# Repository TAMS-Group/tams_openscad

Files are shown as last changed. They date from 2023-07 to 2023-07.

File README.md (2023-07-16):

# tams_openscad

OpenSCAD models and libraries used with our robots.

This package collects 3D-models of robot parts, sensors, and
mechanical components to be used with the OpenSCAD 3D-modelling tool.
Feel free to use and modify as needed for your own robots and tools.

In particular, this package includes a set of common "TAMS flange"
adapter plates that we use to quickly assemble combinations of sensors 
and grippers or specialized tools for experiments. 
The basic idea is to combine a <em>core</em> part permanently 
installed on a robot (or fixed assembly) with different <em>outer</em>
adapter plates for different grippers or experiment setups.

<a href="doc/images/tams_flange_kuka_wsg50.png">
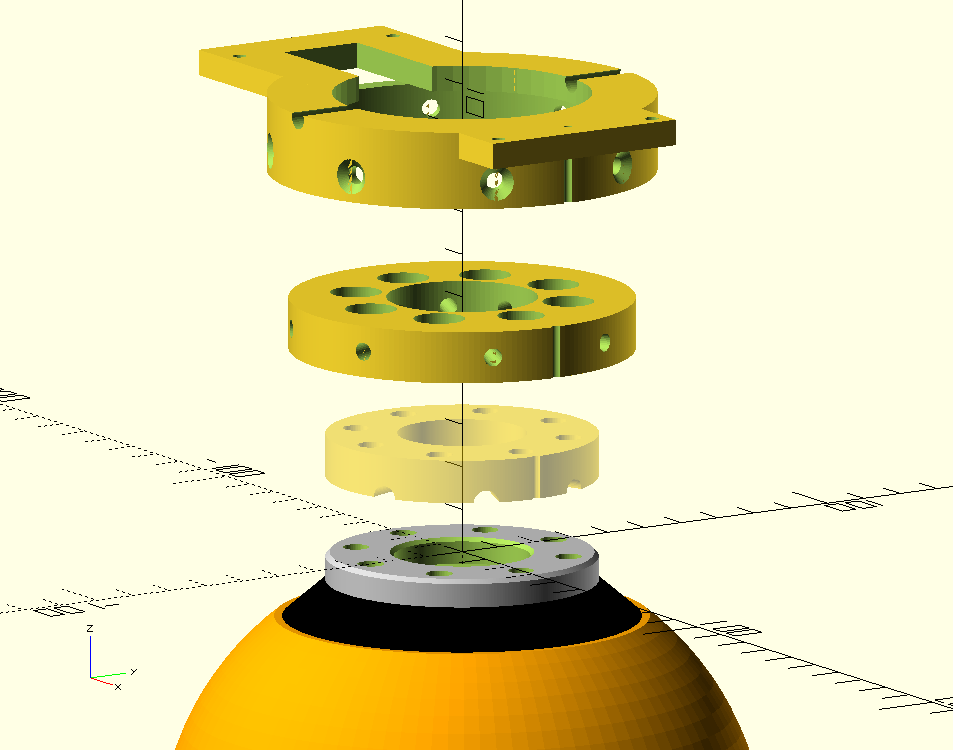
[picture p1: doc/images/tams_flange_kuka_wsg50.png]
TAMS flange adapter for Schunk WSG-50 gripper on Kuka LWR-4+robot
  
</a>

<a href="doc/images/tams_flange_diana_gripper.png">
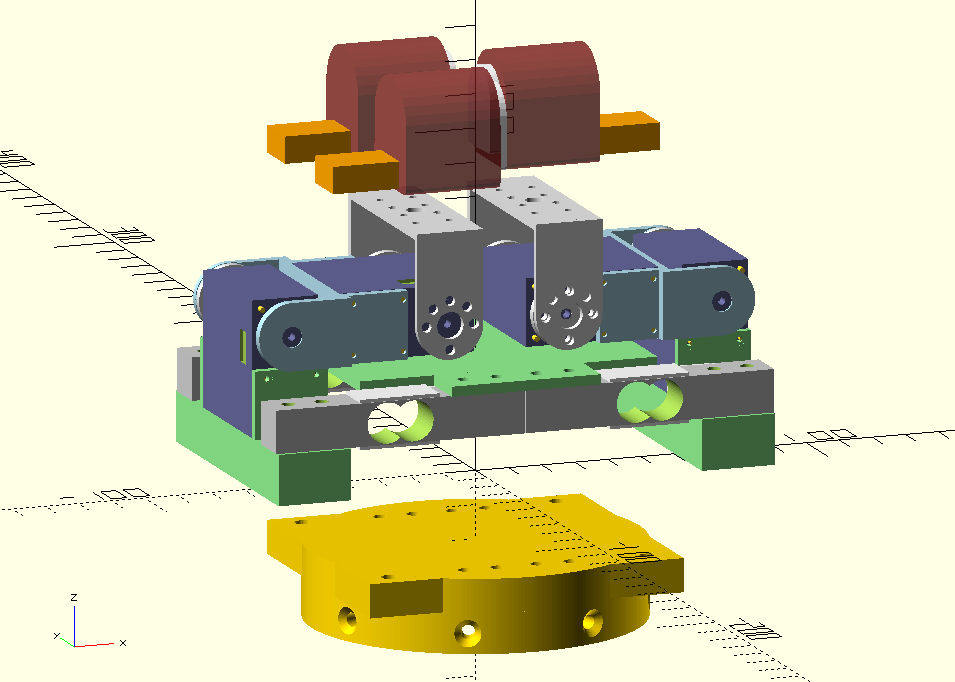
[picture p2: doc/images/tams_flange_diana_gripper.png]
TAMS flange adapter for SCSERVO driven 4-DOF two-finger grippr
  
</a>

We currently use a common size of d=80mm and h=12mm for the core adapters,
which fits the ISO-9409-1-50-4-M6 adapter used on most current cobots
(UR5/UR5e, UR10/UR10e, Kuka LWR4+ iiwa, ...) and the slightly larger
ISO-9409-1-63-4-M6 flange on our Mitsubishi PA10-6C robots.
The outer adapters typically use d=99mm and varying height, depending
on expected payload and tool mounting requirements.

Outer and inner parts are connected with a set of eight radial M4 screws,
so that parts can be mounted or unmounted without disassembly of other
stages or the total robot setup.

There is nothing magical about the values, but they seemed like a promising
combination of required strength/payload and overall size.
To save overall length of the stacked adapters, parts include cavities
to fit the screws/bolts/nuts of the next level.

## Components Overview

This package includes the following <em>core</em> (robot-side) parts:

- UR5/UR5e, UR10/UR10e, LWR4+, iiwa, ... (ISO-9409-1-50-4-M6) flange adapter,
  in three variants: with embedded M4 square nuts, embedded M4 hex nuts,
  or without embedded nuts. The version without embedded nuts is easiest
  to use, but be careful not to over-torque the radial mounting screws.
- Mitsubishi PA10-6C (ISO-9409-1-63-4-M6) flange adapter.
- 3D-printed ISO-9409-1-50-4-M6 compatible adapter (to stack things).

<a href="doc/images/tams_flange_ur5.png">
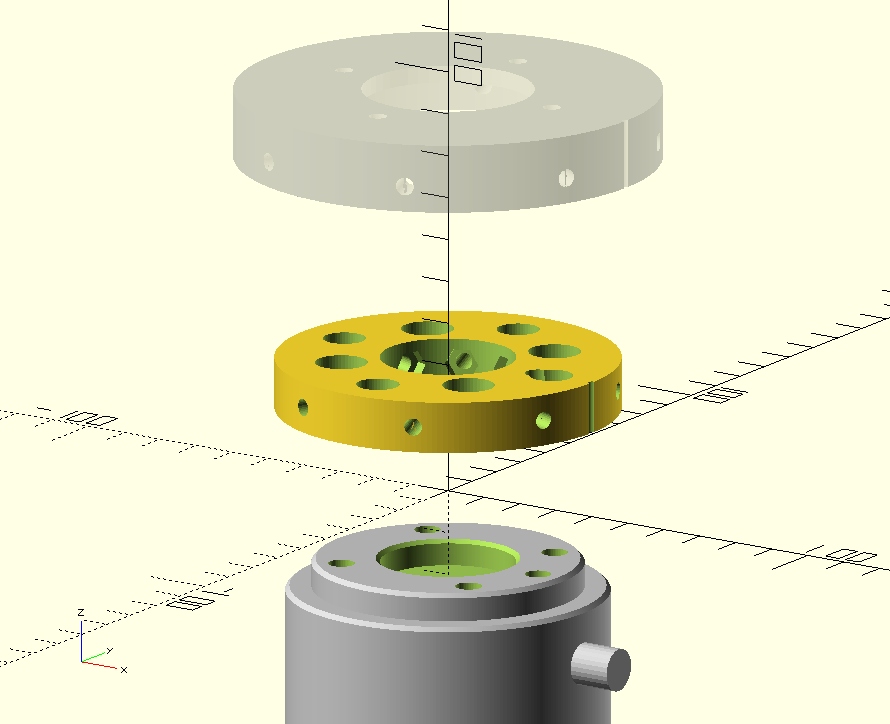
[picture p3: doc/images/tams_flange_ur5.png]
TAMS flange adapter for UR5/UR5e industrial robot
  
</a>

<a href="doc/images/tams_flange_pa10.png">
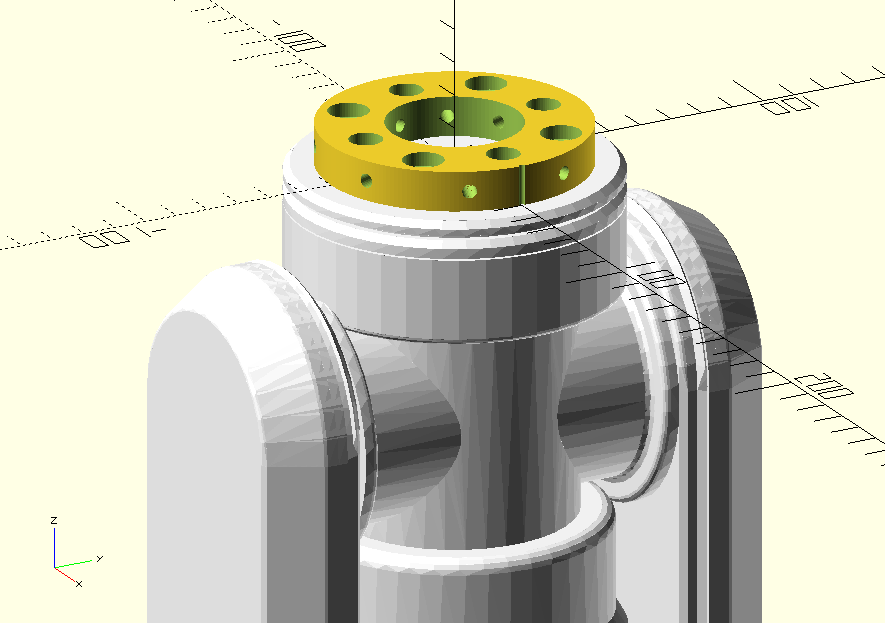
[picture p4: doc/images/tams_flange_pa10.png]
TAMS flange adapter for MHI PA10-6C industrial robot
  

</a>

Force/Torque-sensor (tool-side) <em>core</em> adapters:

- ATi Mini45e.
- Robotiq FTS-150 (soon).
- Sunrise Instruments M3207.

And the corresponding <em>outer</em> adapters for the following tools:

- ATi Nano17e force/torque sensor.
- ATi Mini45e force/torque sensor.
- Robotiq FTS-150 force/torque sensor (soon).
- Sunrise Instruments M3207 force/torque sensor.
- passive weight holder for force/torque sensor calibration.

- Robotiq 3-finger adaptive gripper (aka 3-finger hand).
- Schunk WSG-50 parallel gripper.
- TAMS in-house SCSERVO 4-DOF two-finger gripper.
- TAMS in-house tactile arrays.

- DIGIT tactile sensor.
- generic camera-holder (1/4-inch-20-UNC-thread) (6.35 outer, 5.2mm inner, thread 1.27mm).
- fischertechnik-compatible adapter plate.
- ...

<a href="doc/images/tams_flange_ati_mini45.png">
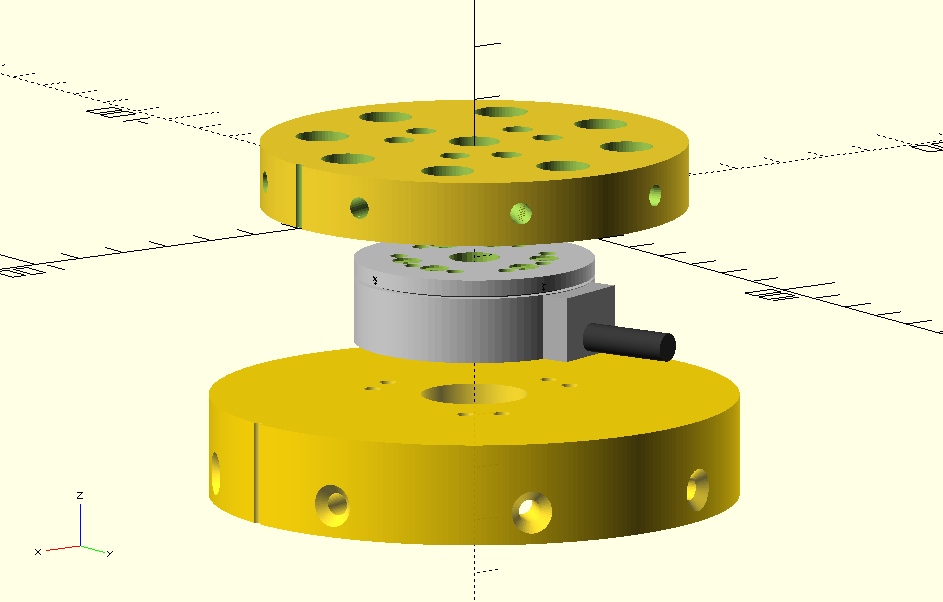
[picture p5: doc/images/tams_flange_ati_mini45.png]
TAMS flange core and outer adapter for ATi mini45e force/torque sensor
  
</a>

<a href="doc/images/tams_flange_fischertechnik.png">
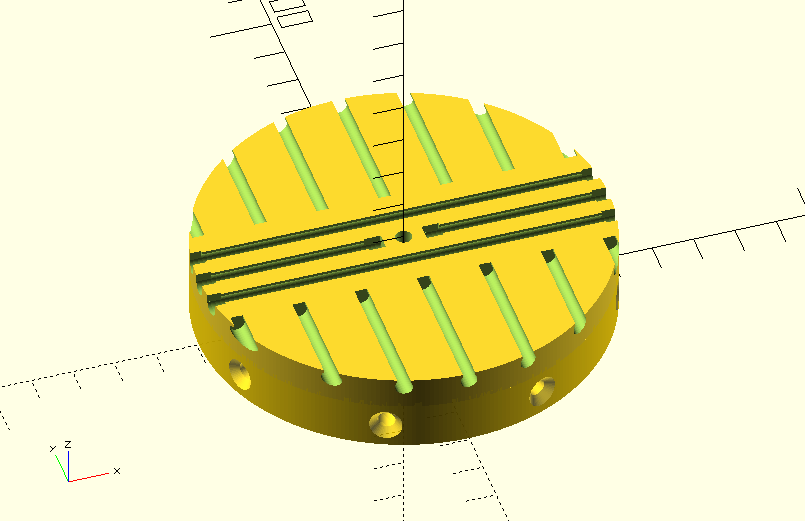
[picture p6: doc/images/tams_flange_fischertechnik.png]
TAMS flange outer adapter for fischertechnik construction set
  
</a>

## Libraries

The package also collects a set of OpenSCAD part libraries that
you might find useful for your own designs:

- <a href="libs/electronics.scad"><tt>electronics.scad</tt></a>,
  a random collection of basic electronic components and common
  Arduino-boards and sensor breakout boards,
- <a href="libs/simple-screws.scad"><tt>simple-screws.scad</tt></a>,
  simplified models of various DIN/ISO-sized screws, nuts, and washers,
- <a href="libs/load_cells.scad"></tt>load_cells.scad</tt></a>,
  geometric models of common load-cells.

<a href="doc/images/electronics.png">
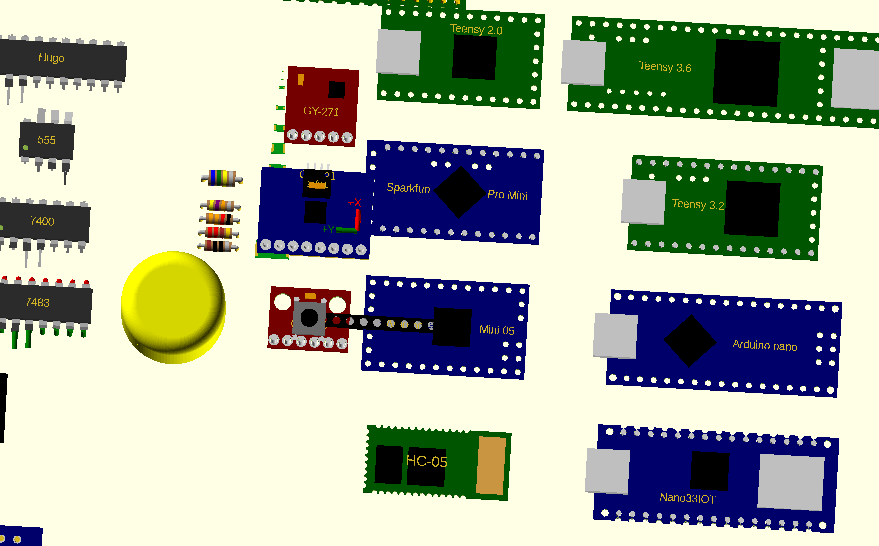
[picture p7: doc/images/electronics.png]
OpenSCAD library of electronics components
  
</a>

<a href="doc/images/load_cells.png">
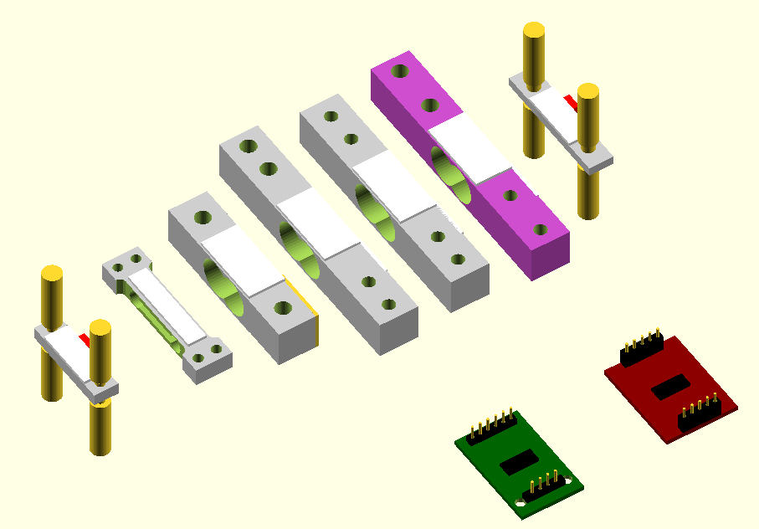
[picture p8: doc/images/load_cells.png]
OpenSCAD library of common load cells
  
</a>

<a href="doc/images/simple_screws.png">
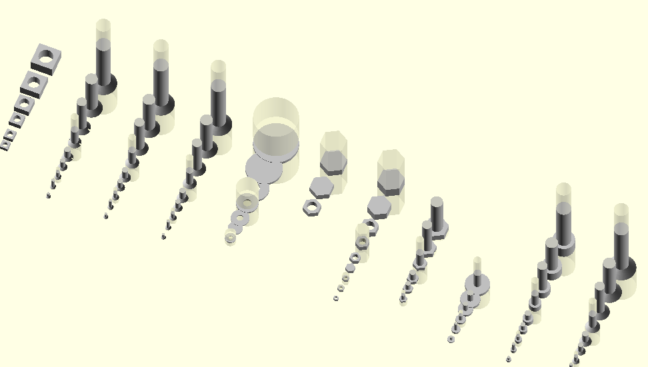
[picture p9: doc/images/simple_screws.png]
OpenSCAD library of DIN/ISO sized screws
  
</a>

## Disclaimer 

In our lab, these plates are used for different short-time experiments,
typically 3D-printed from common PLA/PETG filament with medium infill values. 
However, the parts are clearly not designed for heavy-duty 24/7 industrial use,
and none of the parts have been checked with FEM analysis for mechanical
stress; all dimensions provided just seemed like an acceptable compromise 
for our use cases and relatively low payloads.
In particular, be careful with overloading the parts, as 3D-printed objects
are always prone to delamination and sudden complete breakage.

## Installation

Just download the package. You will need OpenSCAD to open and
modify the provided 3D-models. 
Of course, you will need a 3D-printer to actually produce the adapter plates,
and the usual components (e.g. M3/M4/M6 screws and nuts) to assemble
the different parts.

<!-- preview: grip README.md + firefox localhost:6419 -->

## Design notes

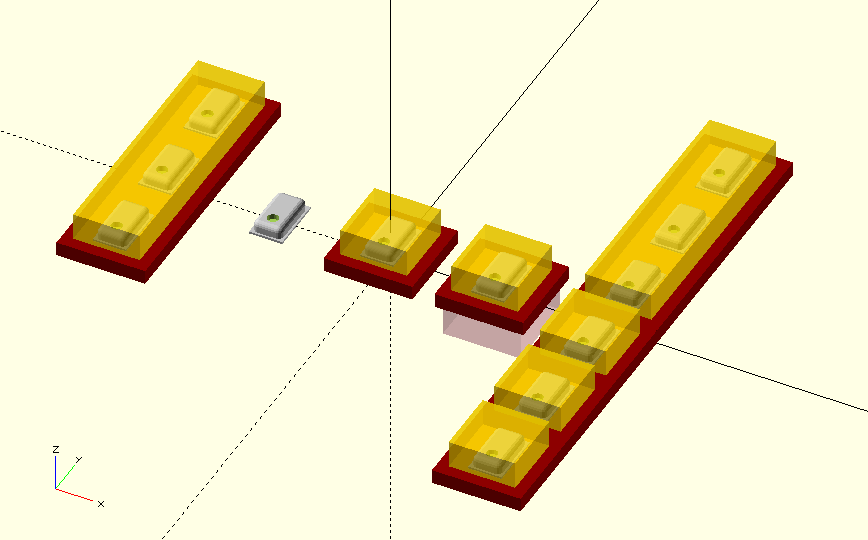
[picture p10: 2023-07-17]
doc/images/takktile.png

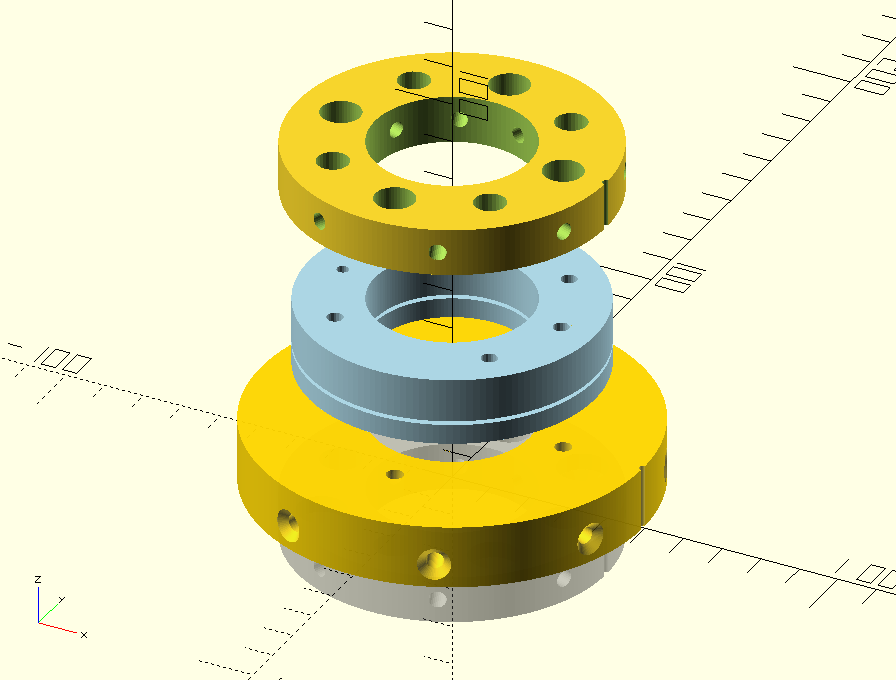
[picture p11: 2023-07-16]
doc/images/tams_flange_sunrise_m3207.png

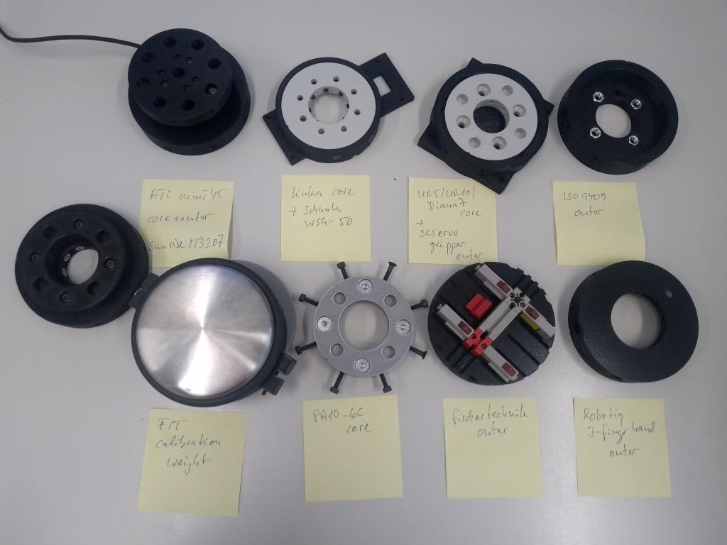
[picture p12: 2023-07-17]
doc/images/tams_flange_family.jpg

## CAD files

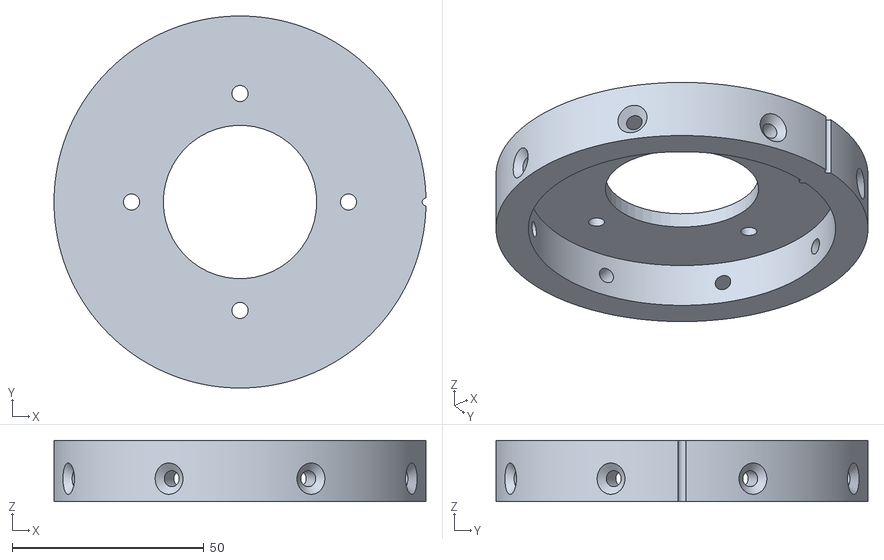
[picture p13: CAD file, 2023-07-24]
meshes/m3207_tams_outer_adapter_80x12_d97.stl
97.0 x 97.0 x 16.0

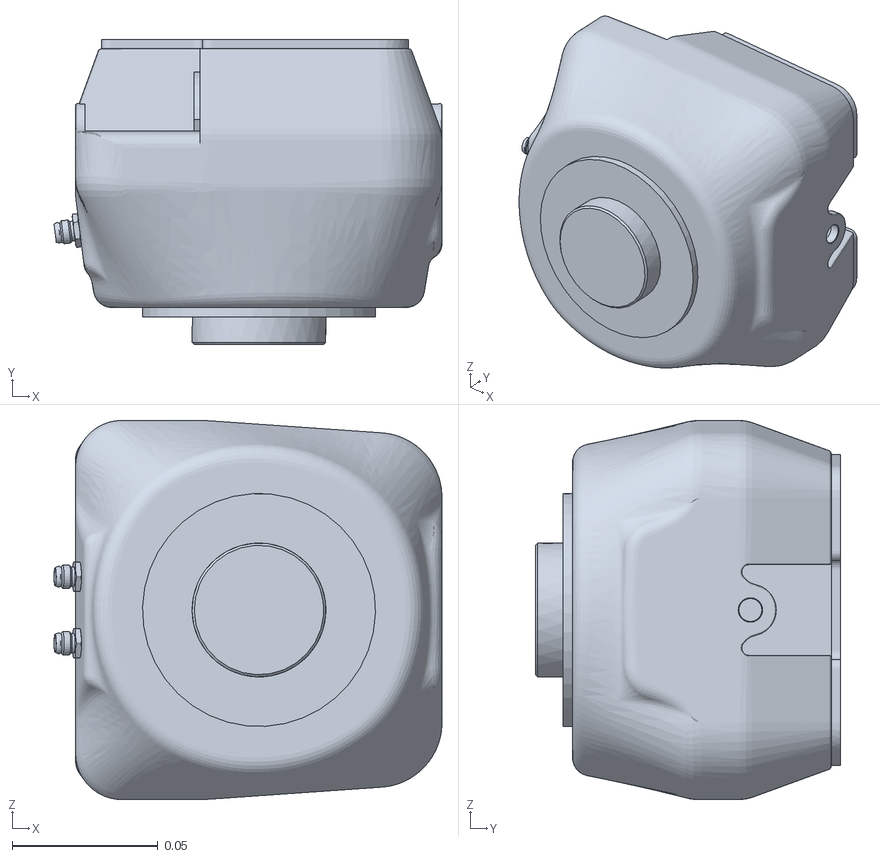
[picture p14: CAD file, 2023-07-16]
robots/robotiq_palm.stl
0.133 x 0.105 x 0.13

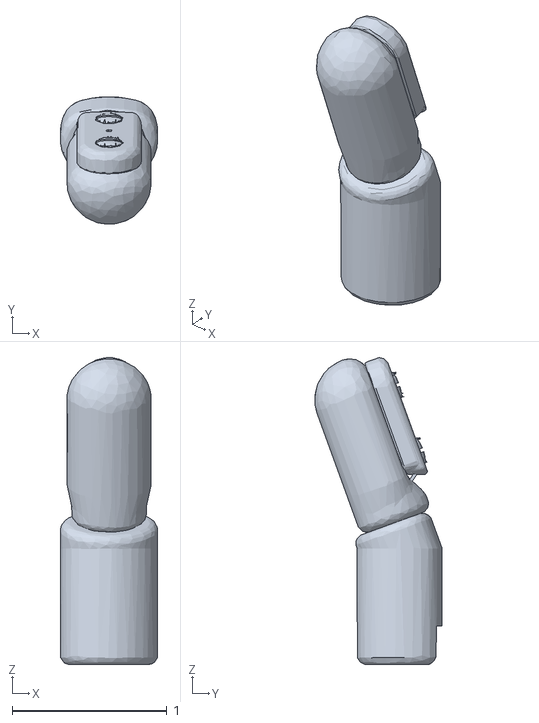
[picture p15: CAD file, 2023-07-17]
sensors/biotac_decimated.stl
0.63 x 0.824 x 1.98

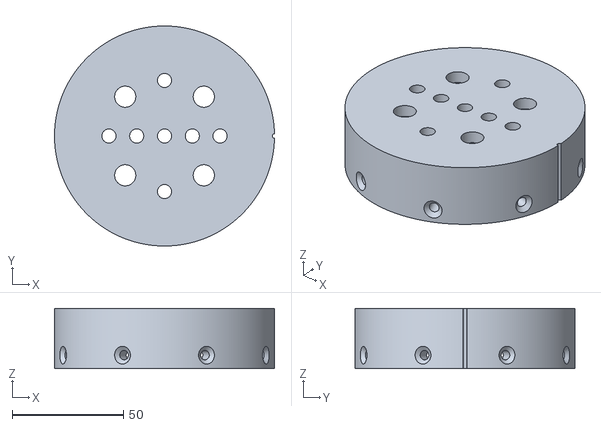
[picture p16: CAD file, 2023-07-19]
meshes/camera_mount_outer_adapter_80x12x15.stl
99.0 x 99.0 x 27.0

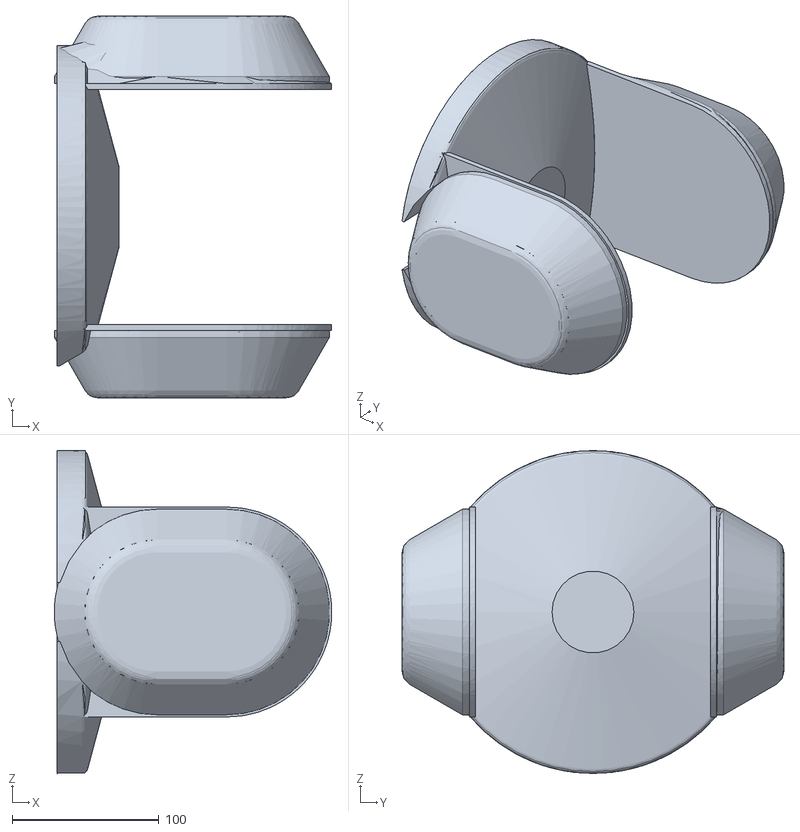
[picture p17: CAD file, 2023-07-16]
robots/pa10s1.stl
189.0 x 260.0 x 220.0

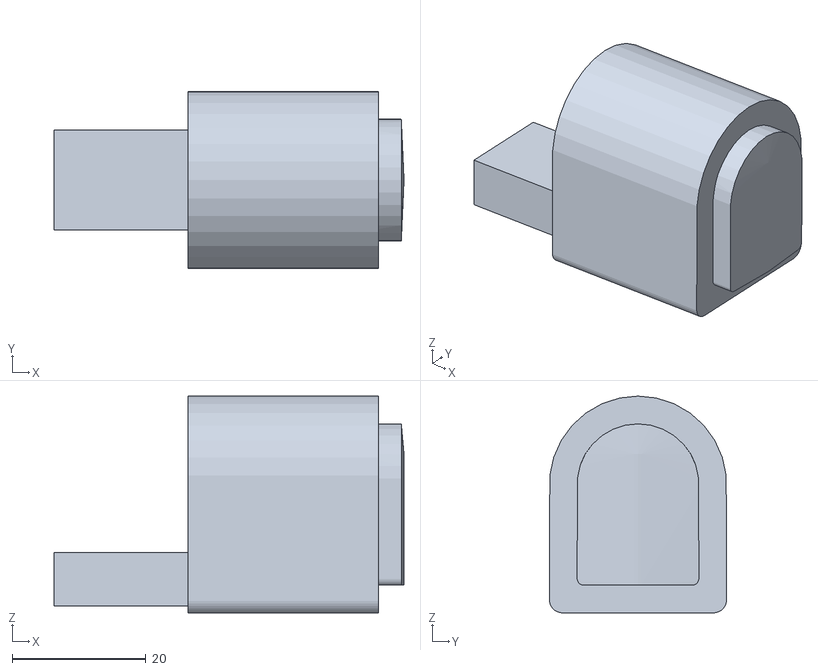
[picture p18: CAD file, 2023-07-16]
sensors/digit_sensor.stl
52.3 x 26.5 x 32.4

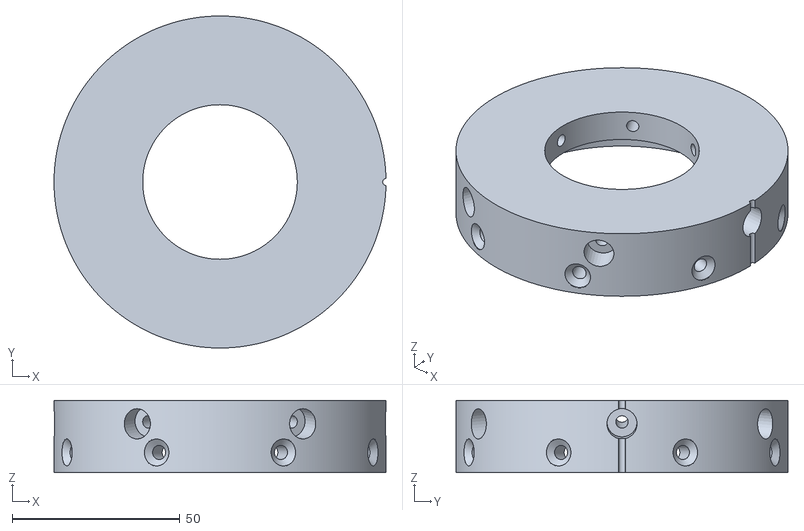
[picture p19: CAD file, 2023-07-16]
meshes/robotiq_3finger_hand_outer_adapter_80x12.stl
99.0 x 99.0 x 21.5

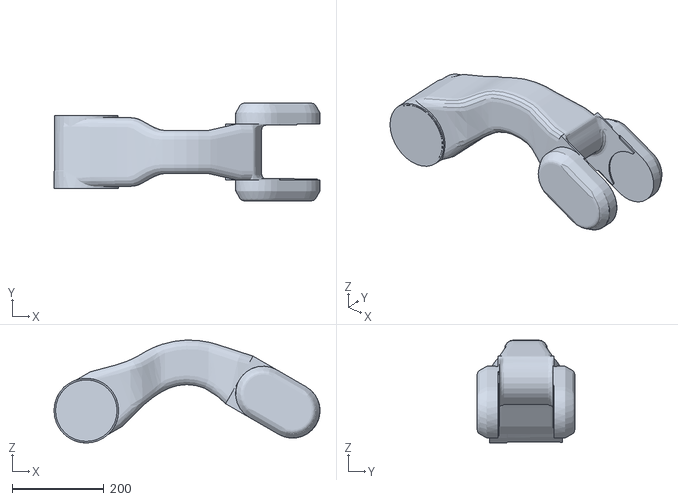
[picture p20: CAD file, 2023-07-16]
robots/pa10s2.stl
580.5 x 213.0 x 224.5

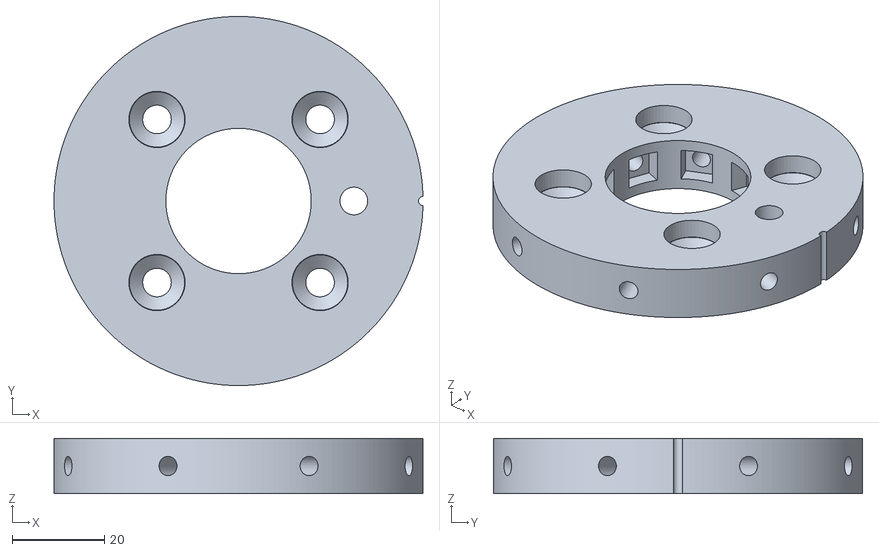
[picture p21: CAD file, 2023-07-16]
meshes/ur5_tams_flange_adapter_80x12_square_nuts.stl
80.0 x 80.0 x 12.0

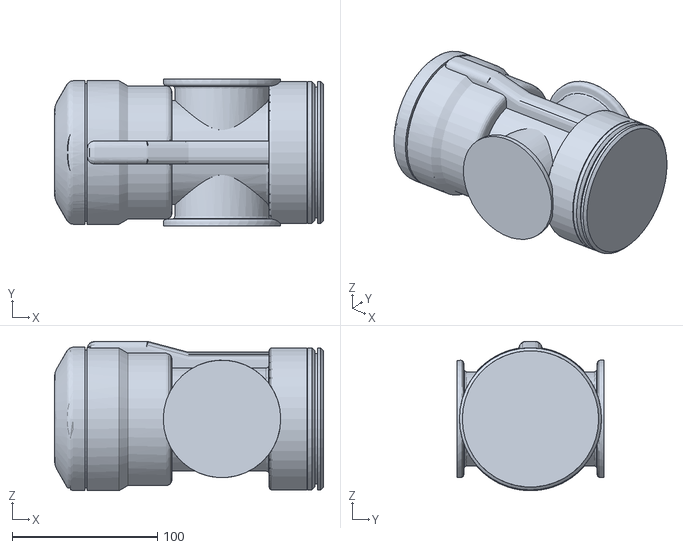
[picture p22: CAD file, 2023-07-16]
robots/pa10w1.stl
185.5 x 101.4 x 103.0

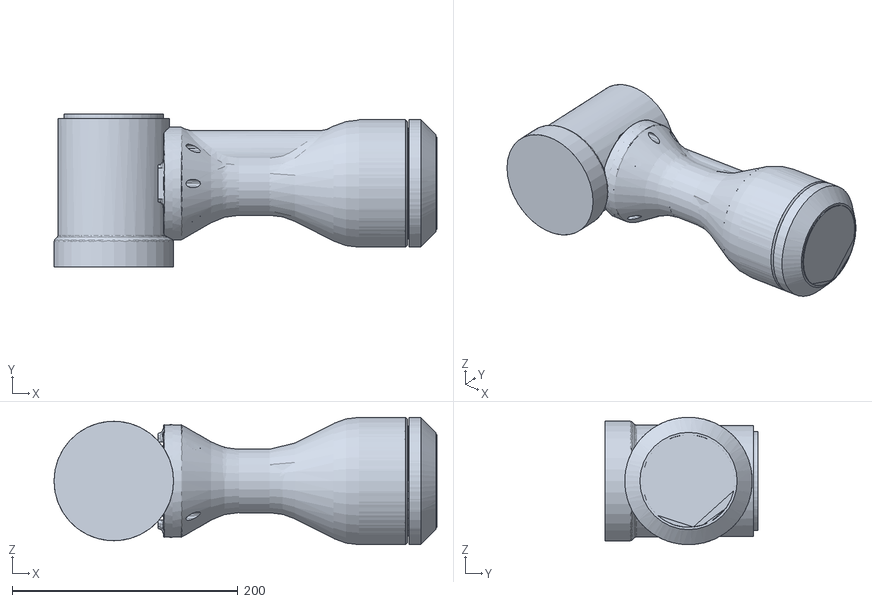
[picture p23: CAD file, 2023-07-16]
robots/pa10e1.stl
339.5 x 135.5 x 112.9

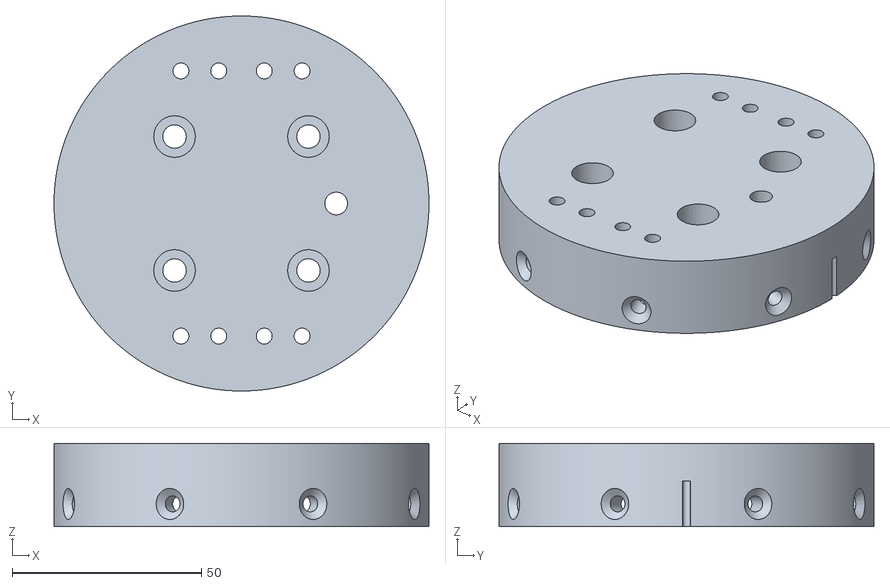
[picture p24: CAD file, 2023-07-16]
meshes/diana_gripper_outer_round_80x12.stl
99.0 x 99.0 x 22.0

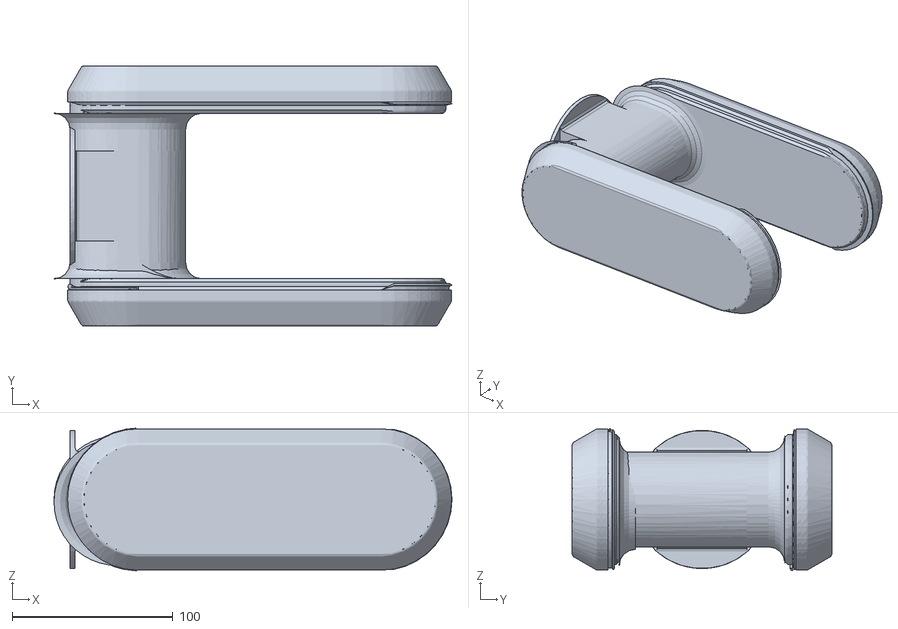
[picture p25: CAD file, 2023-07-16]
robots/pa10e2.stl
247.8 x 162.0 x 88.9

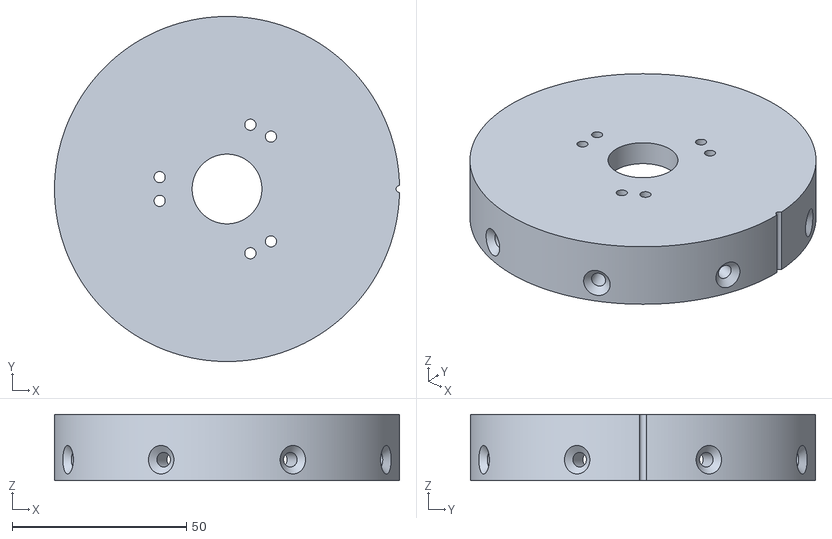
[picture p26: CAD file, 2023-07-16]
meshes/ati45_flange_outer_adapter_80x12x7.stl
99.0 x 99.0 x 19.0

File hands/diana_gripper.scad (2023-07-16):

/** simple four-servo two-finger gripper with mountplate for
 * "TAMS flange" and UR5/Diana7 robots (ISO-9409-...).
 *
 * 2023.07.13 - add "extra_bores" to match our existing (modified) prototype
 * 2022.07.01 - export first meshes (v1)
 * 2022.07.01 - created (based on feetech-servo-hand.scad)
 *
 * (c) 2021, 2022, 2023 fnh, hendrich@informatik.uni-hamburg.de
 */

use <../robots/ur5_flange.scad>
use <../robots/ur5_tams_flange_adapter.scad>
use <../robots/tams_flange_outer_adapter.scad>

use <../sensors/feetech_servo.scad>
use <../sensors/digit_sensor.scad>
use <../libs/load_cells.scad>


translate( [0,0,-100] ) 
  ur5_tool_flange();

color( "red", 0.8 )
rotate( [0,0,0] ) translate( [0,0,-75] ) 
  ur5_tams_flange_adapter( extra_cavities=[0] );




fn = 100;
eps = 0.01;
M6_bore = 6.2;
M4_bore = 4.2;
ee = 30; // "explosion" distance

ddx = 75/2 + 0.2;
ddy = 35;
ddz = 15 + 5 + 12.7/2;

make_diana_flange = 0;
make_gripper_base = 0;

//translate( [0,0,1] ) 
//gripper_base_tams_riser_blocks();
make_gripper_base_tams = 1;

make_palm_plate   = 1;
make_servo_base1  = 1; // first finger
make_connector1   = 1;

make_servo_base2  = 1; // second finger
make_connector2   = 1;

show_loadcells    = 1;

show_servo1P      = 1; // first finger, proximal
show_servo1D      = 1; // first finger, distal
show_bracket1     = 1; // first finger, distal mounting bracket
show_digit1       = 1; // first finger, DIGIT sensor

show_servo2P      = 1; // second finger, proximal
show_servo2D      = 1; // second finger, distal
show_bracket2     = 1; // second finger, distal mounting bracket
show_digit2       = 1; // second finger, DIGIT sensor

if (make_diana_flange) diana_flange();
if (make_gripper_base) gripper_base();

if (make_gripper_base_tams) translate( [0,0,-ee] ) 
  color( "gold" )
  gripper_base_tams();


color( "lightgreen" ) {
if (make_palm_plate)   translate( [0,0, 15+5+12.7] ) palm_plate();
if (make_servo_base1)  translate( [75.0-6-5,0,20] ) servo_base();
if (make_servo_base2)  translate( [-75.0+6+5,0,20] ) servo_base();
}               


if (show_loadcells) {
translate( [ ddx,  ddy, ddz] ) load_cell_komputer_10kg();   
translate( [-ddx,  ddy, ddz] ) load_cell_komputer_10kg();   
translate( [ ddx, -ddy, ddz] ) load_cell_komputer_10kg();   
translate( [-ddx, -ddy, ddz] ) load_cell_komputer_10kg();   
}

if (show_servo1P) {
translate( [75-10,20,50] ) rotate( [0,90,90] ) feetech_scs20_servo( extrude_21mm_axles=0);
translate( [75-10,20+6,50] ) rotate( [0,90,-90] ) feetech_servo_disc( extrude_screws_length=0, extrude_screws_head=[] );
// translate( [75-10,-20-6,50] ) rotate( [0,90,90] ) feetech_servo_disc( extrude_screws_length=0, extrude_screws_head=[] );
}

if (make_connector1) 
translate( [45,1,50] ) rotate( [-90,0,-90] ) // for complete model
// rotate( [-90,0,-90] ) translate( [0,0,-20] ) // for standalone rendering
proximal_medial_connector();

if (show_servo1D) {
translate( [75-10-47,20,50] ) rotate( [-90,0,0] ) feetech_scs20_servo( extrude_21mm_axles=0);
translate( [75-10-47,20+6,50] ) rotate( [0,90,-90] ) feetech_servo_disc( extrude_screws_length=0, extrude_screws_head=[] );
translate( [75-10-47,-20-6,50] ) rotate( [0,90,90] ) feetech_servo_disc( extrude_screws_length=0, extrude_screws_head=[] );
}

if (show_bracket1) 
  translate( [18,0,15+5+30+27.5] ) rotate( [0,180,90] ) 
    feetech_scs_bracket_big();

if (show_digit1) 
translate( [ 18,0,90] ) rotate( [0,0,180]) 
digit_sensor();


if (show_servo2P) {
translate( [-(75-10),20,50] ) rotate( [0,90,90] ) feetech_scs20_servo( extrude_21mm_axles=0);
translate( [-(75-10),20+6,50] ) rotate( [0,90,-90] ) feetech_servo_disc( extrude_screws_length=0, extrude_screws_head=[] );
// translate( [-(75-10),-20-6,50] ) rotate( [0,90,90] ) feetech_servo_disc( extrude_screws_length=0, extrude_screws_head=[] );
}

if (make_connector2) 
translate( [-45,1,50] ) rotate( [90,0,-90] ) proximal_medial_connector();

if (show_servo2D) {
translate( [-(75-10-47),20,50] ) rotate( [-90,180,0] ) feetech_scs20_servo( extrude_21mm_axles=0);
translate( [-(75-10-47),20+6,50] ) rotate( [0,90,-90] ) feetech_servo_disc( extrude_screws_length=0, extrude_screws_head=[] );
// translate( [-(75-10-47),-20-6,50] ) rotate( [0,90,90] ) feetech_servo_disc( extrude_screws_length=0, extrude_screws_head=[] );
}

if (show_bracket2) 
translate( [-18,0,15+5+30+27.5] ) rotate( [0,180,90] ) feetech_scs_bracket_big();

if (show_digit2) {
translate( [-18,-20,90] ) digit_sensor();
translate( [-18,+20,90] ) digit_sensor();
}

/**
 * hardcoded size palm plate, mounts on load-cell screws
 */
module palm_plate( 
  alpha = 0.9,
  dx = 45, dy = 85, dz = 3, dx2=90,
  load_cell = [75.0, 12.7, 12.7],
  bore_offsets = [-16, -6, 6, 16], // relative to center of palm
  M4_bore=4.2, M4_head_diameter = 7.0+1.0, M4_head_length=4+1.0, M4_screw_length=30, 
)
{
  difference() {
    union() {
      translate( [0,0,dz/2] ) 
        cube( [dx, dy, dz], center=true );
      translate( [0,0,dz/2] ) 
        cube( [dx2, dy-2*15, dz], center=true );
    }
    
     // loadcell mounting bores
    for( ddy=[-35, +35] ) { // loadcell y positions
      for( ddx=bore_offsets ) { // loadcell M4 bores
        translate( [ddx, ddy, -dz-eps] ) 
          cylinder( d=M4_bore, h=dz+ddz+2*eps, center=false, $fn=50 );
        translate( [ddx, ddy, -dz-eps] ) 
          cylinder( d=M4_head_diameter, h=M4_head_length, center=false, $fn=50 );
      }
    }

  }
}


module servo_base(
  alpha = 0.9,
  dx = 6+10+6, dy = 85, dz = 15, ddy = 35,
  dty = 2.5, // thickness of servo mounting "towers"
  servoy = 41.1, // some SCservos are slightly wider than 40.0
  load_cell = [75.0, 12.7, 12.7],
  bore_offsets = [-5, 5], // relative to center of servo_base block!
  M4_bore=4.2, M4_head_diameter = 7.0+1.0, M4_head_length=4+1.0, M4_screw_length=30, 
)
{
  difference() {
    union() {
      // main mounting block
      color( "gold", alpha )
      translate( [0,0,-dz/2] )
        cube( [dx,dy,dz], center=true );
      
      // servo mounting "towers"
      color( "gold", alpha )
      for( ddty=[-servoy/2-dty/2, servoy/2+dty/2] ) 
        translate( [0, ddty,10] )
          cube( [dx, dty, 20], center=true );      
    }
    
    // loadcell mounting bores
    for( ddy=[-35, +35] ) { // loadcell y positions
      for( ddx=[-5, 5] ) { // loadcell M4 bores
        translate( [ddx, ddy, -dz-eps] ) 
          cylinder( d=M4_bore, h=dz+ddz+2*eps, center=false, $fn=50 );
        translate( [ddx, ddy, -dz-eps] ) 
          cylinder( d=M4_head_diameter, h=M4_head_length, center=false, $fn=50 );
      }
    }
    
    // servo mounting bores
    translate( [0,20,30-eps] ) rotate( [0,90,90] ) feetech_scs20_servo( extrude_mounting_screws=dty, extrude_mounting_screws_heads=4 
    );
  }
}


module gripper_base(
  alpha = 0.9,
  dx = 90, dy = 85, dz = 15,
  M6_bore=6.2, M6_head_diameter = 10.0+1.0, M6_head_length=7+1.0, M6_screw_length=20,
  M4_bore=4.2, M4_head_diameter = 7.0+1.0, M4_head_length=4+1.0, M4_screw_length=30,
  make_ISO9409_bores = false,
  extra_bores = [[38,36,5],[-39,36,5], [-39,-36,5],[39,-36,5]], // [[x,y,d],[x,y,d],[x,y,d], ...
)
{
  difference() {
    color( "lightgreen", alpha )
    union() {
      // mounting plate for Diana7 flange
      translate( [0,0,dz/2] )
        cube( [dx,dy,dz], center=true );
      
      // riser blocks to mount loadcells, min z-height 3mm for loadcell clearance
      ddz = 5;
      for( dyy =[dy/2-16/2,-dy/2+16/2] )
        translate( [0, dyy,dz+ddz/2] )
          cube( [23+23, 16, ddz], center=true );
    }
    
    // Diana7 M6 D912 screw bores, max length in flange is 12 
    rr = 25.0; 

    if (make_ISO9409_bores) {
      for( phi=[0,90,180,270] ) {
        rotate( [0,0,phi+45] ) translate( [rr,0,-eps] )
          cylinder( d=M6_bore, h=dz+2*eps, center=false, $fn=40 );
        rotate( [0,0,phi+45] ) translate( [rr,0,dz-M6_head_length] )
          cylinder( d=M6_head_diameter, h=M6_head_length+2*eps, center=false, $fn=40 );
      }
    }

    // Diana7 alignment pin bore, max depth in flange in 6
    translate( [rr,0,-eps] )
      cylinder( d=6.0, h=dz+2*eps, center=false, $fn=40 );
    
    // loadcell mount bores
    for( ddy=[-35, +35] ) { // loadcell y positions
      for( ddx=[-16,-6, 6,16] ) { // loadcell M4 bores
        translate( [ddx, ddy, -eps] ) 
          cylinder( d=M4_bore, h=dz+ddz+2*eps, center=false, $fn=50 );
        translate( [ddx, ddy, -eps] ) 
          cylinder( d=M4_head_diameter, h=M4_head_length, center=false, $fn=50 );
      }
    }

    for( i=[0:len(extra_bores)-1] ) {
      echo( "EXTRA_BORES: ", extra_bores[i] );
      ddx = extra_bores[i][0];
      ddy = extra_bores[i][1];
      ddd = extra_bores[i][2];
      translate( [ddx, ddy, -eps] )
        cylinder( d=ddd, h=dz+5, center=false, $fn=40 );
    }
    
  } // difference
}
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

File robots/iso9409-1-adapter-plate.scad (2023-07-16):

/** OpenSCAD model of the ISO-9409-1-50-4-M6 adapter plate,
 * as used on many industrial cobots, e.g. UR3/UR5/UR10, Kuka LWR, ...
 *
 * Based on mechanical drawings from UR documents, plus a low-res scan
 * from research-gate. Dimensions in millimeters.
 * 
 * 2023.03.01 - created
 *
 * (c) 2023 fnh, hendrich@informatik.uni-hamburg.de
 */
 
eps = 0.1;
fudge = 0.1; // FDM overextrusion/shrinking compensation

D1 = 50;   // diameter of screw-bore ring
D2 = 63.0; // outer mounting flange diameter
D3 = 31.5; // diameter of inner bore of mounting flange
N  = 4;    // number of bores
D4 = 6.1;  // M6

translate( [0,0,-15] ) iso9409_1_flange();
translate( [0,0, 15] ) iso9409_1_spacer_ring(); 

 


/* 50-4-M6 robot flange, e.g. LWR-4+, 6mm deep thread bores */
module iso9409_1_flange( D5=90, thickness=15.0, fn=500 ) {
  difference() {
    // main robot tool-flange body
    union() {
      translate( [0,0,0] )
        cylinder( d=90.0, h=thickness-5.0, center=false, $fn=fn );
      translate( [0,0,0] )
        cylinder( d=D2, h=thickness-1, center=false, $fn=fn );     
      translate( [0,0,thickness-1] )
        cylinder( d1=D2, d2=D2-1, h=1, center=false, $fn=fn );     
    }
    // inner bore and extra bevel
    translate( [0,0,thickness+eps-5.0] )
      cylinder( d=D3, h=5.0, center=false, $fn=fn );
    translate( [0,0,thickness+eps-1] )
      cylinder( d1=D3, d2=D3+1, h=1, center=false, $fn=fn );
      
    // screw bores, 6mm deep
    for( alpha=[45,90+45,180+45,270+45] )
      rotate( [0,0,alpha] )
        translate( [D1/2,0,thickness+eps-6.0] )
          cylinder( d=D4, h=6.0, center=false, $fn=100 );
    // through bores, visualization mostly
    for( alpha=[45,90+45,180+45,270+45] )
      rotate( [0,0,alpha] )
        translate( [D1/2,0,-eps] )
          cylinder( d=5.0, h=thickness+2*eps, center=false, $fn=100 );

    // alignment-pin bore
    translate( [D1/2,0,-eps] )
      cylinder( d=6.0, h=thickness+2*eps, center=false, $fn=100 );
  }
}


/**
 * Simple distance ring for the ISO-9409-1-50-4-M6 flange.
 * (For example, use if your screws are a bit too long.)
 */
module iso9409_1_spacer_ring( thickness=4.0, fn=500 ) {
  difference() {
    cylinder( d=D2-fudge, h=thickness, center=false, $fn=fn );    
    translate( [0,0,-eps] )
      cylinder( d=D3+fudge, h=thickness+2*eps, center=false, $fn=fn );
    // screw bores
    for( alpha=[45,90+45,180+45,270+45] )
      rotate( [0,0,alpha] )
        translate( [D1/2,0,-eps] )
          cylinder( d=D4, h=thickness+2*eps, center=false, $fn=100 );
    // alignment-pin bore
    translate( [D1/2,0,-eps] )
      cylinder( d=6.0, h=thickness+2*eps, center=false, $fn=100 );
  }
}

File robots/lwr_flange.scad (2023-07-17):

/** lwr_flange.scad
 * 
 * Simplified models of the Kuka LWR-4+ tool mounting flange and
 * (cable-passthrough) distance plate.
 *
 * 2023.07.03 - created
 *
 * (c) 2023, fnh, hendrich@informatik.uni-hamburg.de
 */
 
 
eps = 0.1;
$fn = 100;
ee = 30; // "explosion" distance, use 0 for STL export
 
 
translate( [0,0,0] ) lwr_tool_flange(); // link7

color( "gold", 0.5 ) translate( [0,0,1*ee-12] ) lwr_distance_plate();

// "TAMS flange" core adapter for the Kuka LWR4+
translate( [0,0,2*ee-12] ) lwr_tams_flange_adapter();

// "TAMS flange" outer adapter for the Schunk WSG-50 gripper
translate( [0,0,3*ee] ) tams_wsg50_adapter();

// Optional traditional mount plate for the WSG-50 
//translate( [0,0,5*ee] ) lwr_wsg50_mount_plate();

// Simplified CAD model of the WSG-50 housing
translate( [0,0,5.5*ee +6 ] ) wsg_50_gripper();

// Optional mounting plate for our "tactile exploration" setup
// use <../sensors/ati_nano17e.scad>
// translate( [0,0,5*ee] ) lwr_ati_nano_plate();



/** simplified model of the LWR4+ tool flange, ISO 9409-1-50-4-M
 *  d_outer = 75, d_flange = 63, d_screws = 50, d_inner = 31.5,
 *  four screws M6 depth 5 (!), 
 *  one alignment pin d=6.
 *  Note that the robot actually has 7 M6 threads, but only
 *  four are specified/used for ISO 9409-1-50-4-M.
 *  Model is centered in x and y, with tool flange at z=0.
 */
module lwr_tool_flange()
{
  d_flange = 63.0; d_screws = 50.0; d_inner = 31.50;
  h_flange = 45.75; h_top = 6.50; h_inner = 6.20; h_bevel = 1.0;
  d_sphere = 140.0;
  h_cone = 15;
  l_screw_bore = 5.0;

  union() {
    // main robot A6+A7 sphere 
    color( "orange" )
    intersection() {
      translate( [0,0,-d_sphere/2] )
        sphere( d=d_sphere, $fn=100 );
      translate( [0, 0, -d_sphere/2-h_cone] )
        cube( [d_sphere, d_sphere, d_sphere], center=true );
    }

    color( "black" )
    translate( [0,0,-h_top-h_cone] )
      cylinder( d1=98, d2=63, h=h_cone, center=false, $fn=300 );
  }
    
  // actual mounting flange with bevel
  difference() {
    color( "silver" ) 
    union() {
      // beveled upper flange
      translate( [0,0,-h_top] )
        cylinder( d=d_flange, h=h_top-h_bevel, center=false, $fn=300 );    
      translate( [0,0,-h_bevel] )
        cylinder( d1=d_flange, d2=d_flange-2*h_bevel, h=h_bevel, center=false, $fn=300 );    
    }

    // beveled inner cutout
    translate( [0,0,-h_inner+eps] )
      cylinder( d=d_inner, h=h_inner, center=false, $fn=300 );   
    translate( [0,0,-h_bevel+eps] )
      cylinder( d1=d_inner, d2=d_inner+2*h_bevel, h=h_bevel, center=false, $fn=300 );   
    
    // four + three M6 bores, depth 6
    for( alpha=[45,90,135,180,225,270,315] ) {
      rotate( [0,0,alpha] ) translate( [d_screws/2,0,-l_screw_bore+eps] ) 
        cylinder( d=6.2, l_screw_bore, center=false, $fn=50 );
    } 

    // alignment pin bore
    rotate( [0,0,0] ) translate( [d_screws/2,0,-6.20+eps] ) 
      cylinder( d=6.00, h=6.20, center=false, $fn=100 );
  }
}


module lwr_distance_plate()
{
  hh = 10.0; d_outer = 63.0; d_screws = 50.0; d_inner = 30;
  l_screw_bore= 5.0;
  difference() {
    cylinder( d=d_outer, h=hh, center=false, $fn=300 );

    translate( [0,0,-eps] )
      cylinder( d=d_inner, h=hh+2*eps, center=false, $fn=300 );

    // four + three M6 through bores
    for( alpha=[45,90,135,180,225,270,315] ) {
      rotate( [0,0,alpha] ) translate( [d_screws/2,0,-eps] ) 
        cylinder( d=6.2, hh+2*eps, center=false, $fn=50 );
    } 

    // alignment pin through bore
    rotate( [0,0,0] ) translate( [d_screws/2,0,-eps] ) 
      cylinder( d=6.00, h=hh+2*eps, center=false, $fn=100 );

    // three radial cable channels (on bottom)
    for( alpha = [-67.5, -22.5, 22.5, 67.5] )
      rotate( [0,0,alpha] ) translate( [d_outer/2,0,-eps] ) 
        rotate( [0,90,0] ) 
          cylinder( d=6, h=d_outer, center=true, $fn=50 );

    // +x "notch" (only in model)
    translate( [d_outer/2, 0, -eps] )
      cylinder( d=2.0, h=hh+2*eps, center=false, $fn=20 );
  }
} // lwr_distance_plate


/**
 * Model of our universal "TAMS LWR" tool flange adapter.
 * Outer diameter of 80mm is chosen to be compatible with 
 * the Mitsubishi PA10-6C robot flange (which is slightly larger 
 * in diameter than UR5/UR10/LWR4+/Diana/...).
 * 
 * Optional, we add h_base mm of height to the adapter to make space
 * for the radial (inside-to-outside) cable channels in the original
 * Kuka ("media interface") distance plate.
 *
 * 2023.07.03 created
 */
module lwr_tams_flange_adapter(
  d_outer  = 80.0,  // adapter plate outer diameter
  d_screws = 50.0, // diameter of mounting screws positions
  d_inner  = 35.0, // diameter of inner wire-through hole (Kuka only has 28)
  h_base   =  0.0, // optional extra base height for cable passthroughs
  h_core   = 12.0, // effective "TAMS" plate thickness
  make_screws = false,   // include fake screws
  extra_cavities = [[0], 25.0, 11, 6],   // [[angles], r_outer, d_cavity, h_cavity]
  // extra_cavities = [[0,90,180,270], 28.8, 10, 7],
) 
{
  M6 = 6.2;
  screw_inner_diameter = M6;
  screw_head_diameter = 2*M6; 

  n_outer_drill_holes = 8;
  
  //color( [0.8,0.7,0.6] )
  difference() {
    // actual adapter plate
    cylinder( d=d_outer, h=h_base+h_core, center=false, $fn=200 );
    
    // inner boring for tools and wires
    translate( [0, 0, -eps] )
      cylinder( d=d_inner, h=h_base+h_core+2*eps, center=false, $fn=100 );    

    // four+three LWR mounting screws M6, thread depth 5.0, 
    // countersunk screws DIN 7991 lengths are 8 10 12 14 16 18 20 ... 
    // at plate height 5+12 we can have l=16mm
    // 
    for( alpha=[45,90,135,180,225,270,315] ) {
      rotate( [0, 0, alpha] ) 
        translate( [d_screws/2, 0, h_core+h_base-7+3*eps] ) 
          rotate( [0, 180, 0] ) 
            screw_M6_10_countersunk( length=(10+h_base), extra_height=5 );
    }

    // LWR alignment pin bore
    translate( [d_screws/2, 0, -eps] )
      cylinder( d=6.0, h=h_base+h_core+2*eps, center=false, $fn=50 );
    
    // radial screws, eight M4 drill holes, diameter shrinks to the inside
    for( i=[0:1:(n_outer_drill_holes-1)] ) {      
      rotate( [0, 0, 22.5+i*360.0/n_outer_drill_holes] ) 
        translate( [d_outer/2, 0, h_base+h_core/2 ] ) 
          rotate( [0,-90,0] ) 
            cylinder( d1=4.2, d2=4.0, h=(d_outer-d_inner)/2+1, center=false, $fn=30 );
    }

    // three radial cable channels (on bottom)
    if (h_base > 0.0) {
      for( alpha = [-67.5, -22.5, 22.5, 67.5] )
        rotate( [0,0,alpha] ) translate( [d_outer/2,0, 1-eps] ) 
          rotate( [0,90,0] ) 
            cylinder( d=5.5, h=d_outer, center=true, $fn=50 );
     }

    // alignment notch at +x
    translate( [d_outer/2, 0, -eps] )
      cylinder( d=2.0, h=h_core+h_base+2*eps, center=false, $fn=50 );

    // optional axial cavities to fit next-state mounting plates
    if (len(extra_cavities) > 1) {
      angles = extra_cavities[0];
      echo( angles );
      nn = len(angles);
      rr = extra_cavities[1]; // radius to cavity
      dd = extra_cavities[2]; // cavity diameter
      zz = extra_cavities[3]; // cavity depth
      for( angle=angles ) {      
        rotate( [0, 0, angle] ) 
          translate( [rr, 0, h_base+h_core-zz ] ) 
            cylinder( h=zz+eps, d=dd, center=false, $fn=50 );
      }
    } // if
  }
} // lwr_tams_flange_adapter



module lwr_ati_nano_plate()
{
  M6 = 6.0;
  hh = 5;
  // ATi nano17e sensor diameter and length
  d_ati_nano17  = 17;     // diameter of ATi nano-17 sensor
  l_ati_nano17  = 14.5;   // body length of ATi nano-17 sensor
  
  difference() {
    // adapter plate for Kuka LWR
    // outer diameter 63mm
    cylinder( d=63, h=hh, center=false, $fn=300 );

    // one M6 "pass-stift" hole for exact alighment (unused by us), radial offset r=25
    translate( [25, 0, -eps] ) 
      cylinder(d=M6, h=hh+2*eps, $fn=100, center=false );
    
    // four M6 screw holes on LWR mounting plate, radial offset r=25 
    // r=25
    for( phi=[45, 135, 225, 315] ) {
      rotate( [0,0,phi] ) {
        translate( [25, 0, 1] ) 
          rotate( [180, 0, 0] )
            screw_M6_10_countersunk( length=10, extra_height=2+5 );
            // cylinder(d=M6, h=hh+2*eps, $fn=$fn, center=false );
      }
    } 
    translate( [0,0,-eps] ) cylinder( d=d_ati_nano17, h=hh+2*eps, center=false, $fn=100 );  
  }
  
  ati_nano17e_base_mounting_plate( h=hh, inbus=false, inbus_head_height=hh-2 );
}



module screw_M6_10_countersunk( length=10, extra_height=3 ) {
  M6 = 5.5;   // actual thread diameter
  dk = 11.5;  // outer head diameter
  k  = 3.0;   // head height
  // standard rim length seems to be 1 mm on M6
  union() {
    translate( [0,0,-k-extra_height+eps] ) cylinder( d=dk+0.5, h=extra_height, center=false, $fn=$fn );
    translate( [0,0,-k] ) cylinder( r1=dk/2, r2=M6/2, h=k, center=false, $fn=$fn );
    translate( [0,0,-eps] ) cylinder( d=M6, h=length, center=false, $fn=$fn );
  }
}
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

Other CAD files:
robots/pa10base.stl
meshes/diana_gripper_outer_adapter_with_corner_bores.stl
meshes/pa10_tams_flange_80x12.stl
meshes/diana7_tams_flange_adapter_80x12.stl
robots/pa10_tams_flange_adapter.scad
meshes/ati45_tams_flange_adapter_80x12.stl
meshes/diana_gripper_riser_blocks.stl
meshes/digit_tams_outer_adapter_80x12.stl
meshes/digit_tams_outer_adapter_tower.stl
meshes/digit_tams_outer_adapter_unprintable.stl
meshes/fischertechnik_outer_adapter_80x12.stl
meshes/iso9409_flange_outer_adapter_80x12_h10.stl
meshes/lwr_tams_flange_adapter_80x12.stl
meshes/m3207_tams_flange_adapter_80x12.stl
meshes/tams_wsg50_adapter_80x12.stl
meshes/ur5_flange_alignment_pin_6x10.stl
meshes/ur5_tams_flange_adapter_80x12.stl
meshes/ur5_tams_flange_adapter_80x12_hex_nuts.stl
misc/fischertechnik_adapter.scad
robots/robotiq_3finger_hand_adapter.scad
robots/tams_flange_outer_adapter.scad
robots/ur10_flange.scad
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

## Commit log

2023-07-16 Add robot meshes and (simplified) OpenSCAD models.
    [iso9409-1-adapter-plate.scad, lwr_flange.scad, pa10_tams_flange_adapter.scad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]
2023-07-16 Add OpenSCAD exported "TAMS flange" meshes.
    [ati45_flange_outer_adapter_80x12x7.stl, ati45_tams_flange_adapter_80x12.stl, diana7_tams_flange_adapter_80x12.stl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]
2023-07-16 Add OpenSCAD model of SCSERVO four-finger gripper.
    [diana_gripper.scad]
2023-07-16 Add Sunrise M3207 sensor model and adapter plates.
    [sunrise_m3207.scad]
2023-07-16 Add ATi mini45 f/t sensor and DIGIT tactile sensor.
    [ati_mini45e.scad, digit_sensor.scad, digit_sensor.stl]
2023-07-16 Add Feetech SCS-series servo models.
    [feetech_servo.scad]
2023-07-16 Update simple_screws library name.
    [ur5_tams_flange_adapter.scad]
2023-07-17 Simplified 3D model of the Syntouch Biotac sensor.
    [biotac.scad, biotac_decimated.stl]
2023-07-17 Add model of the ATi nano17e force/torque sensor.
    [ati_nano17e.scad, lwr_flange.scad]
2023-07-17 Add photo of 3D-printed parts.
2023-07-17 Add model of Polhemus liberty 6-DOF sensor.
    [polhemus_liberty_sensor.scad]
2023-07-17 Add model of Takktile and Takkstrip sensors.
    [takktile.scad]
2023-07-17 Add screenshot of Takktile sensor model.
2023-07-19 Fix screw positions, countersunk outer screws.
    [m3207_tams_outer_adapter_80x12_d97.stl, sunrise_m3207.scad]
2023-07-19 Add "bone" option to 3D-print sensor stub with real skin.
    [biotac.scad]
2023-07-19 Add generic (1/4 + 3/8 inch) camera mount adapter.
    [camera_mount_outer_adapter.scad, camera_mount_outer_adapter_80x12x15.stl]
2023-07-19 Removed (use updated version instead).
    [m3207_flange_outer_adapter_80x12.stl]
2023-07-19 Add outer plate with fischertechnik-compatible slots.
    [fischertechnik_adapter.scad]
2023-07-24 Add angle-offsets for screws and alignment notch.
    [sunrise_m3207.scad]
2023-07-24 Reverse to M3207 screws at 0 degrees offset.
    [m3207_tams_outer_adapter_80x12_d97.stl]
